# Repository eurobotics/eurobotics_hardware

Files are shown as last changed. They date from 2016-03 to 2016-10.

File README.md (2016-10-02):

# EuRobotics Engineering Hardware
Hardware del equipo Eurobotics Engineering para el desarrollo de robots participantes en Eurobot.

<p align="center">
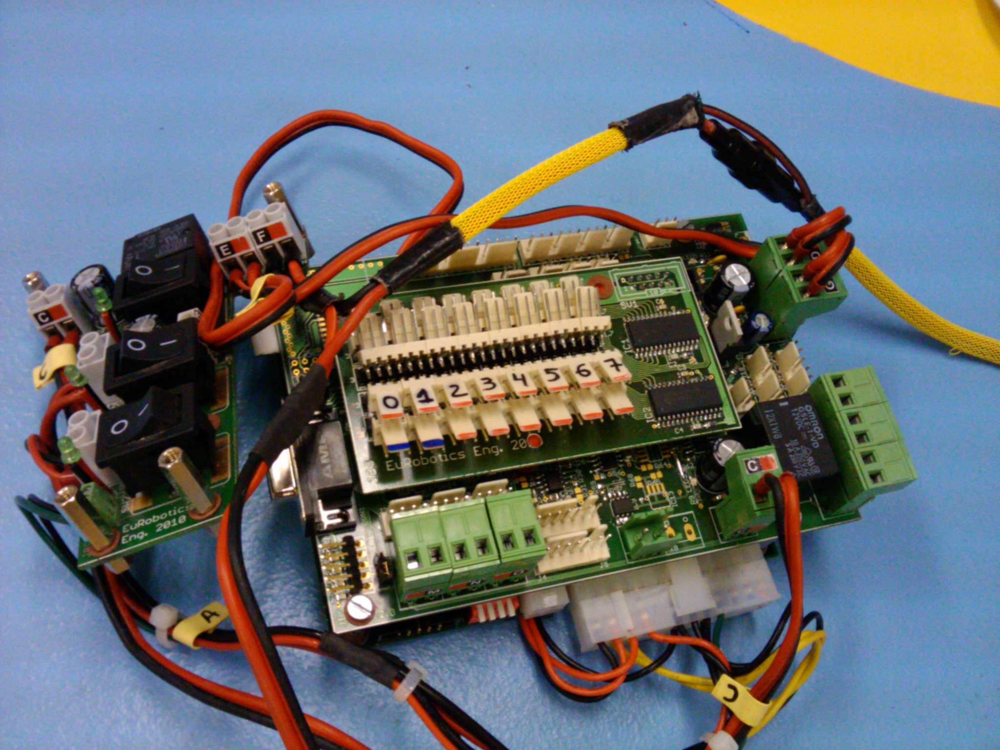
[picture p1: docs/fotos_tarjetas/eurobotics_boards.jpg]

</p>

## Organización

 - Cada carpeta del repositorio se corresponde con una tarjeta.

 - En el root de cada capeta se encuentra el proyecto de desarrollo de la tarjeta (Eagle, Orcad, Altium...). Si es una tarjeta comercial la documentación dada por el fabricante.

 - Por lo general, los archivos de cada proyecto se nombran como MMMMM_rXX, donde XX es la revisión y MMMMM el nombre de la tarjeta. La modificaciones sobre tarjetas fabricadas se documentan añadiendo al nombre del fichero de diseño el sufijo _NNNN_rYY_, donde NNNN es el identificador de la modificacion y YY es el número revisión de la modificación. Por ejemplo: "mainboard_r15_eurobot2012_r1.pdf" es la modificación para eurobot 2012 con revisión 1 de la tarjeta mainboard correspondientes a la revisión 15 de los esquemas.

 - Cada carpeta de una tarjeta desarrollada puede contener las siguientes subcarpetas:
   + bom: listado de materiales.
   + cam: ficheros de fabricación y versión en pdf de versiones de tarjetas fabricadas o de modificaciones en placa realizadas para una edición concreta de Eurobot.

## dsPIC Protoboard

Tarjeta prototipo basada en microcontrolador dspic33. Desarrollada para Eurobot 2010. Diseñada en Eagle (sólo esquematicos). Fabricada sobre tarjeta de prototipos. Es la tarjeta que se utilizó en el robot prototipo, llamado Dumybot, con el que se portó las librerías Aversive.

<p align="center">
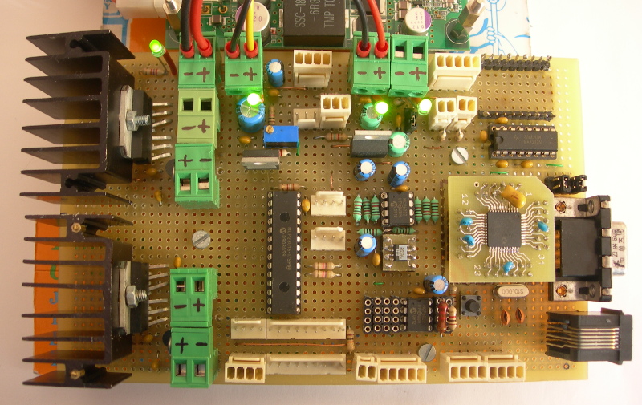
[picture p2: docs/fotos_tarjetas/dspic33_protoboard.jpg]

</p>

### Características

* Control motores: DC, Dunkermotoren, servos, AX12.
* Comunicaciones: RS-232, BT, SPI, I2C
* Sensores: industriales, TTL, laser analógico y encoders en cuadratura
* GPIOS: puerto de expansión I2C de 16 E/S.

### Autor

Javier Baliñas Santos

## Mainboard V01/V02

Tarjeta principal del robot. Compuesta por dos microcontroladores dspic33 comunicados por I2C, un maestro y un esclavo. El maestro está pensado para implementar la navegación motriz y estrategia del robot, y el
esclavo para controlar la mecánica del robot.

<p align="center">
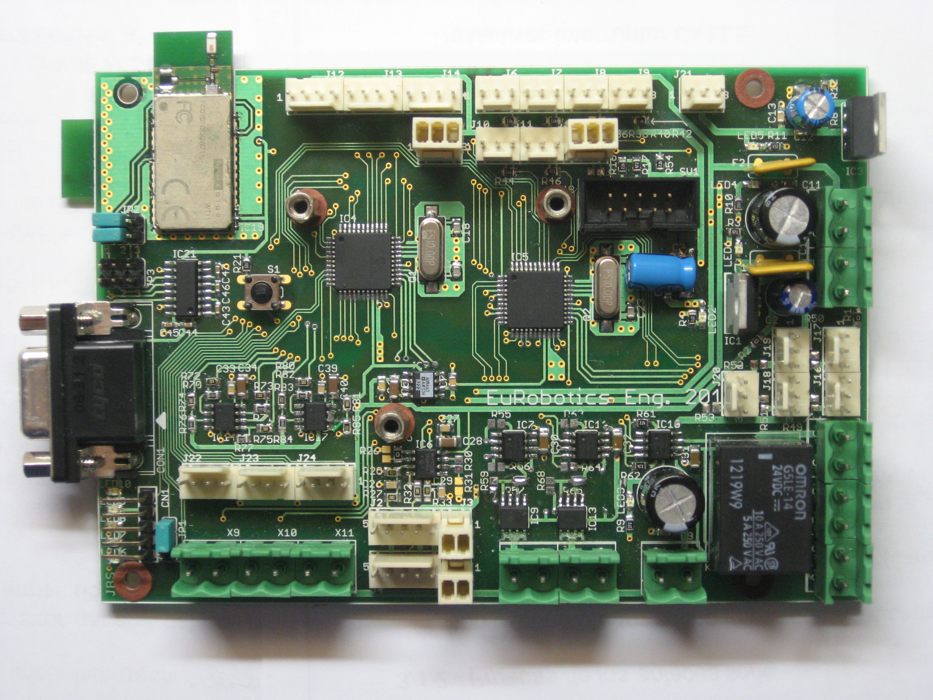
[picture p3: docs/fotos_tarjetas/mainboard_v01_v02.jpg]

</p>

Desarrollada para el robot de Eurobot 2010. Diseño en Eagle (esquemáticos y PCB). Tiene varios bugs documentados y solucionados en la versión 2.

La versión V02 de la tarjeta principal soluciona algunos errores de la versión V01. Desarrollada para Eurobot 2012 y utilizada en las ediciones posteriores.

### Características

* 3 motores Dunkermotoren
* 2 motores DC de 12V
* 1 solenoide 12V
* 1 relé
* 2 telémetros lásers
* 5 servos estándar
* 1 interfaz servos AX12
* 3 encoders con salida en cuadratura
* 7 sensores 12V
* 1 interfaz RS-232
* 2 interfaces Bluetooth (SPP)
* 1 conector para tarjeta de sensores _sensorboard_

### Autor

Javier Baliñas Santos

## Mainboard V03

Tercera versión de la tarjeta principal de los robots. Compuesta por un único un microcontrolador.

Desarrollada para Eurobot 2014 y utilizada en las ediciones posteriores.

<p align="center">
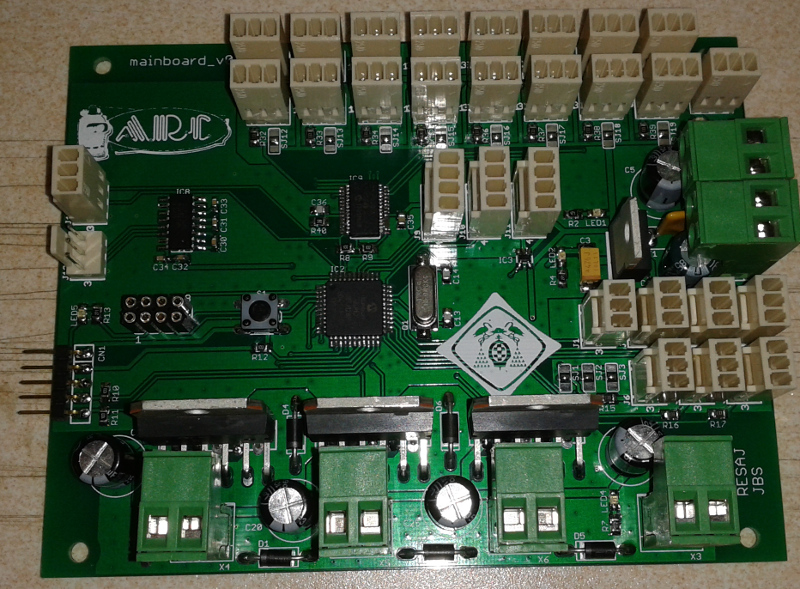
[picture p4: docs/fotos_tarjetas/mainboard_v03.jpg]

</p>

### Características
* 3 motores DC de 12V
* 4 servos estándar
* 1 interfaz servos AX12
* 2 encoders con salida en cuadratura
* 1 encoder con salida en cuadratura (módulo x4, sin decodificación de signo)
* 16 E/S de 12/5V
* 2 entradas de captura de tiempo
* 1 interfaz RS-232/Bluetooth
* 1 interfaz I2C
* 1 interfaz SPI

### Autores

Diseño electrónico: Javier Baliñas Santos  
Diseño PCB: Rubén Espino San José

## Sensorboard

Tarjeta de expansión E/S digital por I2C (32 E/S). Desarrollada para Eurobot 2010 y reutilizada en las siguientes ediciones.

<p align="center">
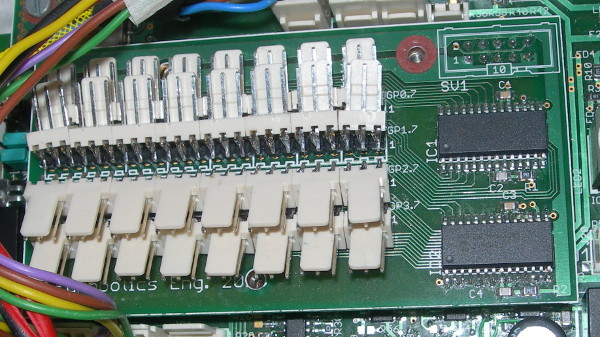
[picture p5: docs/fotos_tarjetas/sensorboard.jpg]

</p>

### Autor

Javier Baliñas Santos

## Swithboard

<p align="center">
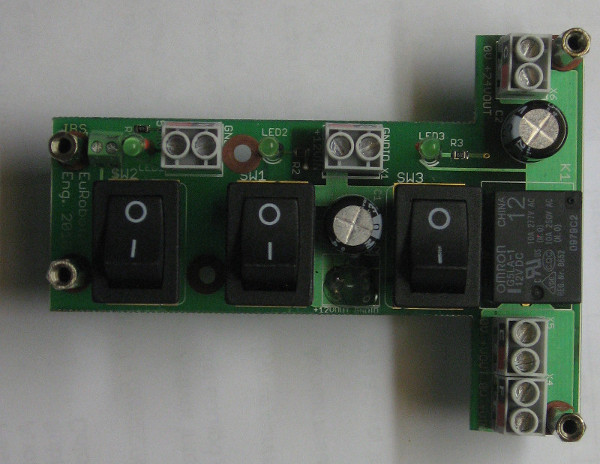
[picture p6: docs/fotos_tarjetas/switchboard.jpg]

</p>

Tarjeta de distribución de alimentación de los robots. Permite activar de forma independiente las diferentes alimentaciones del robot: 24V, 12V y 5V. Desarrollada para Eurobot 2010 y reutilizada en las siguientes ediciones. Diseño en Eagle (esquemáticos y PCB).

### Autor

Javier Baliñas Santos

## Beaconboard

Electrónica de la baliza desarrollada para Eurobot 2010 por Diego Salazar. Permite el control de 1 motor DC con encoder en cuadratura, la lectura de 2 sensores de tipo Keyence y de 2 sensores opticos de herradura. Permite la comunicación por Bluetooth. Tiene bugs resueltos en placa, pero no todos documentados. Diseño en Orcad (esquemas y PCB).

<p align="center">
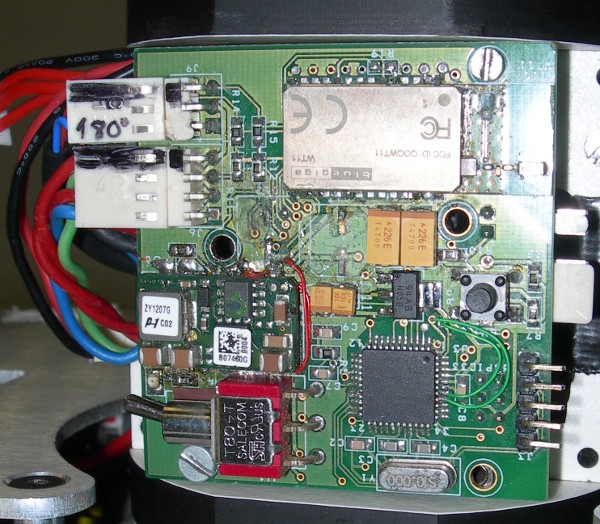
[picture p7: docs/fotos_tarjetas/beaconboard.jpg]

</p>

### Autor

Diego Salazar Arcucci

## Vacuumboard

Tarjeta de control de hasta 4 electrovalvulas y 4 bombas de vacio.

<p align="center">
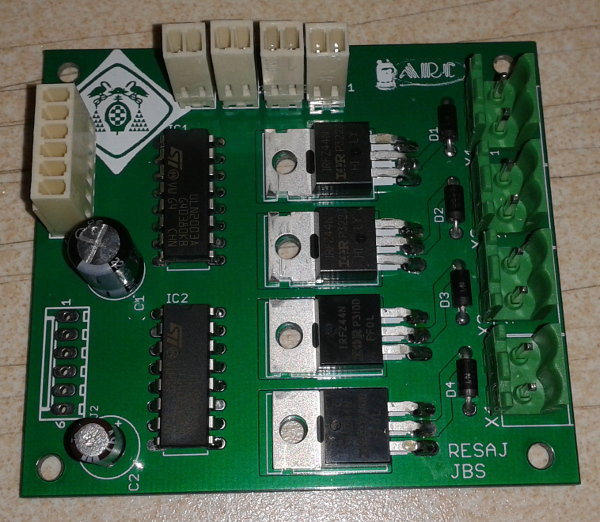
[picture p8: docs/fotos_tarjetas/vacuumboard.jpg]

</p>

### Autores

Diseño electrónico: Javier Baliñas Santos  
Diseño PCB: Rubén Espino San José

## M4 ATX

Fuente de alimentación mini ATX. Perminte un rango de alimentación variable y da salidas de +/-12V, 5V y 3.3V.  Se ha utilizado desde Eurobot 2010 para alimentar la electrónica del robot a partir de baterías. Es una tarjeta comercial.

<p align="center">
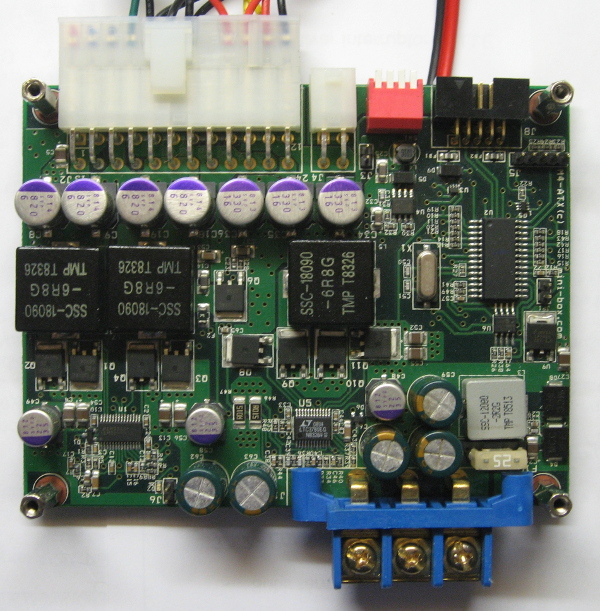
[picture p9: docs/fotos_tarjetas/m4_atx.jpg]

</p>

## Licencia

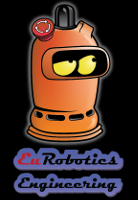
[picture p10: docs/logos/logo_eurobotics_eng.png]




Todos estos productos están liberados mediante [Creative Commons Attribution-ShareAlike 4.0 International License](http://creativecommons.org/licenses/by-sa/4.0/).  
_All these products are released under [Creative Commons Attribution-ShareAlike 4.0 International License](http://creativecommons.org/licenses/by-sa/4.0/)._

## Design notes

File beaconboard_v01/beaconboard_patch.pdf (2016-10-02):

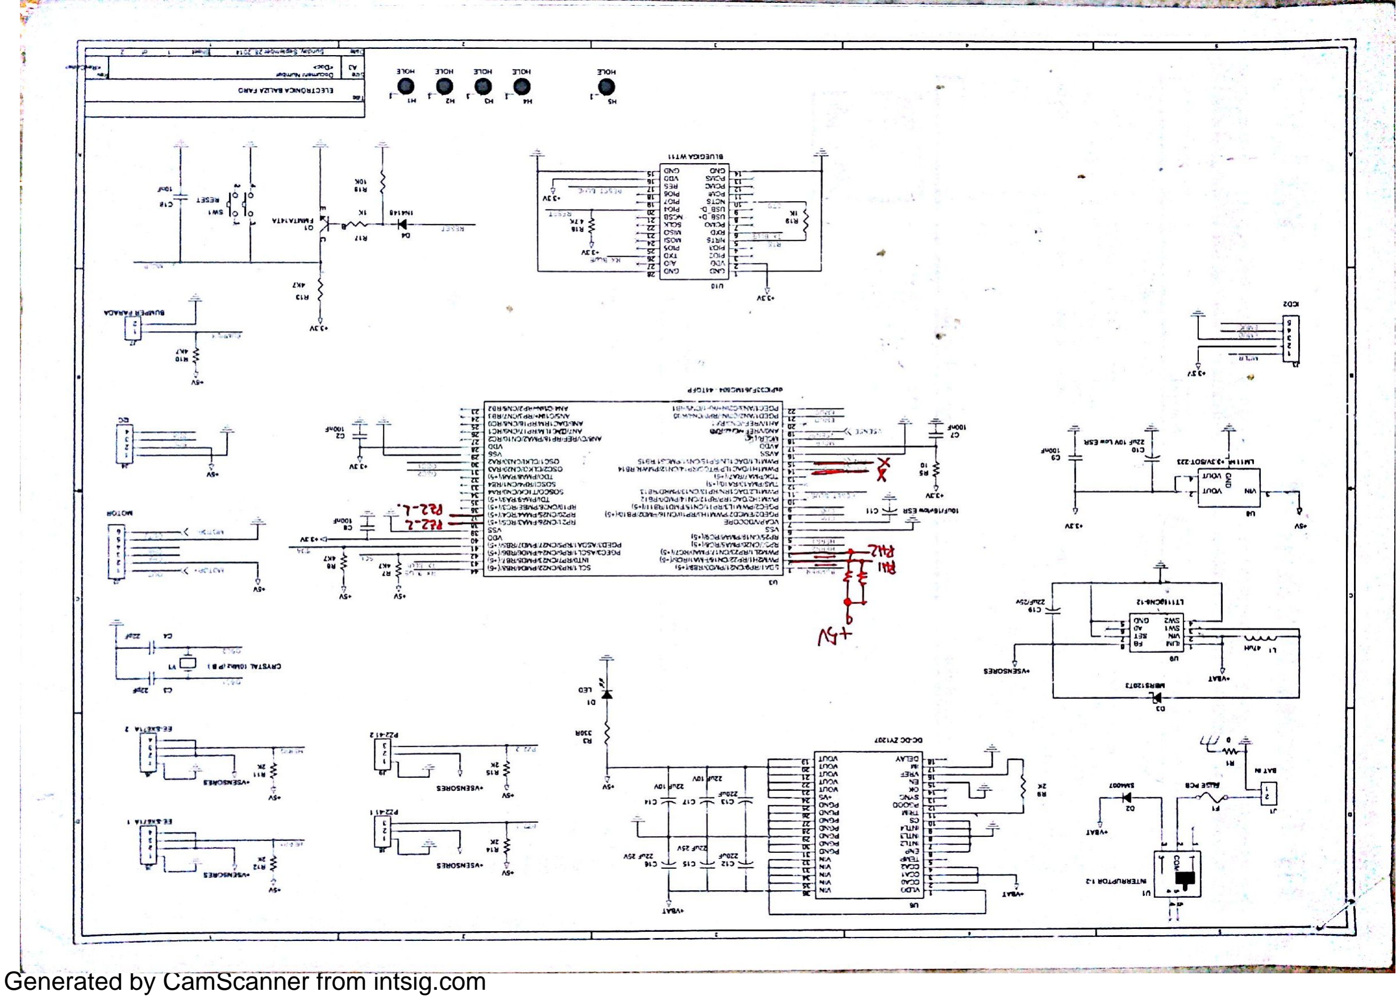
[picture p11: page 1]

Generated by CamScanner from intsig.com

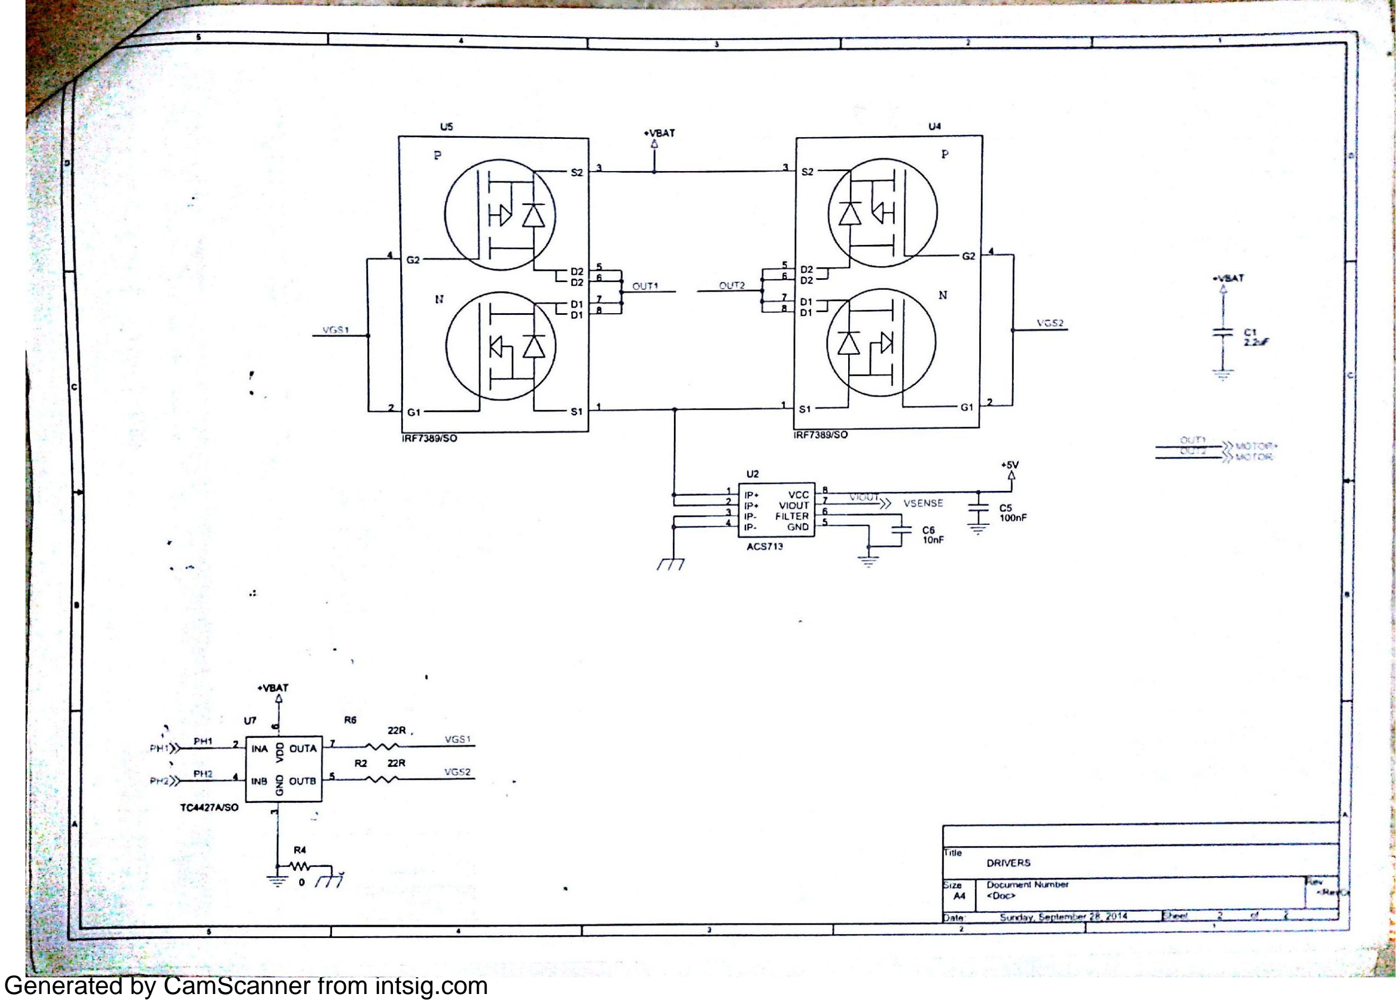
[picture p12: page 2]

Generated by CamScanner from intsig.com

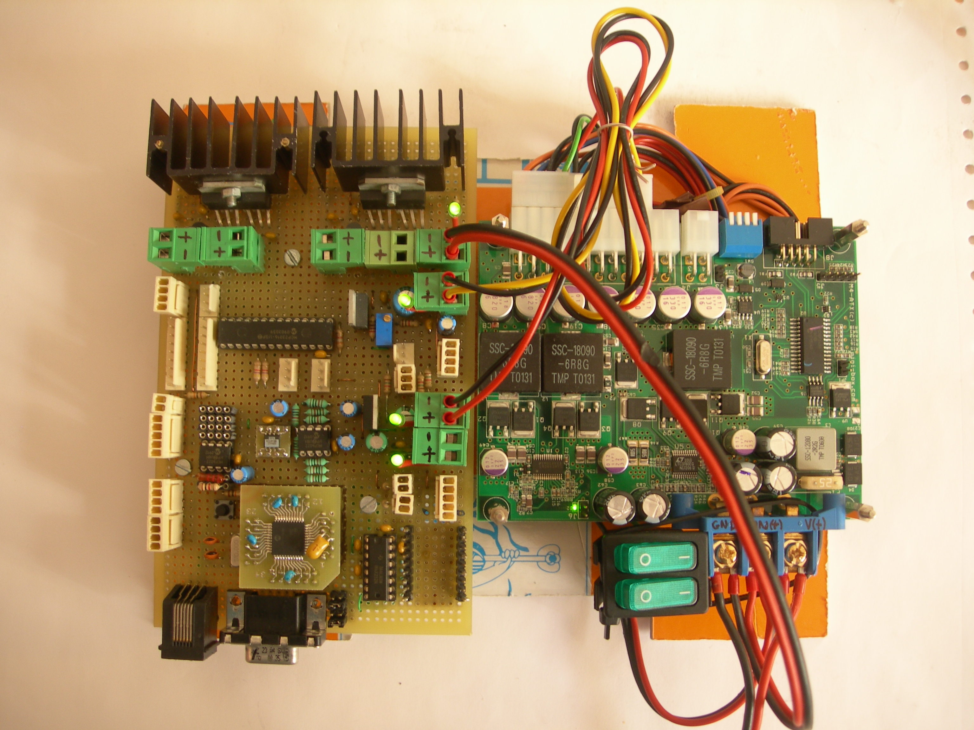
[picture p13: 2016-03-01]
dspic33_protoboard/cam/dvk_dspic33_protoboard.JPG

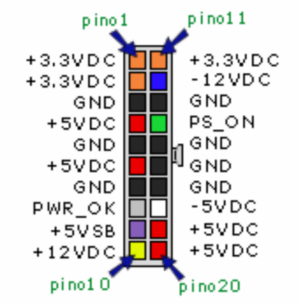
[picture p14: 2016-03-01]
m4_atx/conector_atx.png

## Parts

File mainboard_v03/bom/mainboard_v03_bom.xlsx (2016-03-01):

Qty | Parts | Columna1 | Value | Package | Description | Manufacturer | Manufacture Part # | Supplier | Supplier Part # | Min Qty | Price (EUR) | Ext. Qty | Ext. Price
1 | C1 |  | 220uF/10V | E2,5-7 | CONDENSADOR ELECTROLITICO / 10V / PASO 2.5mm |  |  | symbol |  |  |  | 1 | 0
8 | C10, C11, C12, C30, C31, C32, C33, C34 |  | 100nF | C0603 | CONDENSADOR CERAMICO / 50V / SMD 0603 |  |  |  |  |  |  | 8 | 0
2 | C13, C14 |  | 22pF | C0805 | CONDENSADOR CERAMICO / 50V / SMD 0805 |  |  |  |  |  |  | 2 | 0
3 | C15, C20, C25 |  | 220uF/48V | E3,5-10 | CONDENSADOR ELECTROLITICO / 48V / PASO 3.5mm |  |  | symbol |  |  |  | 3 | 0
3 | C16, C21, C26 |  | 220nF | C0805 | CONDENSADOR CERAMICO / 50V / SMD 0805 |  |  |  |  |  |  | 3 | 0
6 | C17, C18, C22, C23, C27, C28 |  | 15nF | C0805 | CONDENSADOR CERAMICO / 50V / SMD 0805 |  |  |  |  |  |  | 6 | 0
3 | C19, C24, C29 |  | 10nF | C0805 | CONDENSADOR CERAMICO / 50V / SMD 0805 |  |  |  |  |  |  | 3 | 0
5 | C2, C4, C6, C8, C35 |  | 100nF | C0805 | CONDENSADOR CERAMICO / 50V / SMD 0805 |  |  |  |  |  |  | 5 | 0
1 | C3 |  | 47uF/6V | SMC_D | CONDENSADOR TANTALO / 6V / SMD SMC-D |  |  | symbol |  |  |  | 1 | 0
1 | C36 |  | 33pF | C0805 | CONDENSADOR CERAMICO / 50V / SMD 0805 |  |  |  |  |  |  | 1 | 0
2 | C5, C7 |  | 220uF/35V | E5-10,5 | CONDENSADOR ELECTROLITICO / 35V / PASO 5mm |  |  | symbol |  |  |  | 2 | 0
1 | C9 |  | 10uF/6V/lowESR | SMC_A | CONDENSADOR TANTALO / 6V / SMD SMC-A |  |  | symbol |  |  |  | 1 | 0
1 | CN1 |  |  | SIP-100-5V | TIRA DE PINES MACHO ACODADA / PCB |  |  |  |  |  |  | 1 | 0
6 | D1, D2, D3, D4, D5, D6 |  | BYW100 | F126-10 | DIODO DE RECUPERACIÓN RÁPIDA |  |  |  |  |  |  | 6 | 0
2 | F1, F2 |  | FUSETE5 | TE5 | FUSIBLE REARMABLE / 1A / PASO 5mm |  |  |  |  |  |  | 2 | 0
1 | IC1 |  | LM1086CT-3.3 | 317TS | REGULADOR DE VOLTAJE |  |  |  |  |  |  | 1 | 0
1 | IC2 |  | DSPIC33FJ128MC804-I/PT | TQFP44 | MICROCONTROLADOR / TQFP44 |  |  |  |  |  |  | 1 | 0
1 | IC3 |  | SN74LVC1G86DBVR | SOT23-5 | PUERTA LOGICA XOR / SOT23 |  |  |  |  |  |  | 1 | 0
3 | IC4, IC5, IC6 |  | L6203 | MULTIWATT-11 | DRIVER PUENTE EN H MOSFET |  |  |  |  |  |  | 3 | 0
1 | IC7 |  | WT11A | WT11 | MODULO BLUETOOTH |  |  |  |  |  |  | 1 | 0
1 | IC8 |  | MAX232ACSE | SO16 | TRASNCEIVER RS-232 / SO16 |  |  |  |  |  |  | 1 | 0
1 | IC9 |  | MCP23016SS | SSOP28 | EXPANSON DE PUERTOS I2C / SSOP28 |  |  |  |  |  |  | 1 | 0
26 | J1, J2, J3, J4, J5, J6, J7, J8, J12, J13, J26, J27, J28, J29, J30, J31, J32, J33, J34, J35, J36, J37, J38, J39, J40, J41 |  |  | 6410-03 | CONECTOR MOLEX / 3 VIAS / PCB VERTICAL / PASO 2.54mm |  |  |  |  |  |  | 26 | 0
26 | J1, J2, J3, J4, J5, J6, J7, J8, J12, J13, J26, J27, J28, J29, J30, J31, J32, J33, J34, J35, J36, J37, J38, J39, J40, J41 |  |  | 6410-03 | CONECTOR MOLEX / 3 VIAS / CABLE / PASO 2.54mm |  |  |  |  |  |  | 26 | 0
3 | J9, J10, J11 |  | 22-27-2041-04 | 6410-04 | CONECTOR MOLEX / 4 VIAS / PCB VERTICAL / PASO 2.54mm |  |  |  |  |  |  | 3 | 0
5 | LED1, LED2, LED3, LED4, LED5 |  | Green | CHIP-LED0805 | LED VERDE / SMD 0805 |  |  |  |  |  |  | 5 | 0
1 | Q1 |  | 10MHz | HC49UP | CRYSTAL 10.000MHz / SMD HC49UP |  |  |  |  |  |  | 1 | 0
3 | R1, R3, R5 |  | 0R | R0805 | RESISTENCIA / 5% / 0.1W / SMD 0805 |  |  |  |  |  |  | 3 | 0
3 | R10, R11, R12 |  | 10K | R0805 | RESISTENCIA / 5% / 0.1W / SMD 0805 |  |  |  |  |  |  | 3 | 0
3 | R15, R16, R17 |  | 13K | R0805 | RESISTENCIA / 5% / 0.1W / SMD 0805 |  |  |  |  |  |  | 3 | 0
3 | R18, R20, R22 |  | 0R | M0805 | RESISTENCIA / 5% / 0.1W / SMD 0805 |  |  |  |  |  |  | 3 | 0
3 | R19, R21, R23 |  | 12R | M0805 | RESISTENCIA / 5% / 0.1W / SMD 0805 |  |  |  |  |  |  | 3 | 0
1 | R2 |  | 470R | R0805 | RESISTENCIA / 5% / 0.1W / SMD 0805 |  |  |  |  |  |  | 1 | 0
16 | R24, R25, R26, R27, R28, R29, R30, R31, R32, R33, R34, R35, R36, R37, R38, R39 |  |  | R0805 | RESISTENCIA / 5% / 0.1W / SMD 0805 |  |  |  |  |  |  | 16 | 0
2 | R4, R13 |  | 270R | R0805 | RESISTENCIA / 5% / 0.1W / SMD 0805 |  |  |  |  |  |  | 2 | 0
1 | R40 |  | 3K9 | R0805 | RESISTENCIA / 5% / 0.1W / SMD 0805 |  |  |  |  |  |  | 1 | 0
4 | R6, R8, R9, R14 |  | 1K | R0805 | RESISTENCIA / 5% / 0.1W / SMD 0805 |  |  |  |  |  |  | 4 | 0
1 | R7 |  | 2K7 | R0805 | RESISTENCIA / 5% / 0.1W / SMD 0805 |  |  |  |  |  |  | 1 | 0
1 | S1 |  |  | B3F-10XX | PULSADOR CUELLO CORTO / TIPO DPST (DOBLE CIRCUITO PULSACION ÚNICA) |  |  |  |  |  |  | 1 | 0
19 | SJ1, SJ2, SJ3, SJ4, SJ5, SJ6, SJ7, SJ8, SJ9, SJ10, SJ11, SJ12, SJ13, SJ14, SJ15, SJ16, SJ17, SJ18, SJ19 |  | 4K7 | SJ_2 | RESISTENCIA / 5% / 0.1W / SMD 0805 |  |  |  |  |  |  | 19 | 0
1 | SV1 |  | SPI/RF24 | MA04-2 | TIRA DE PINES HEMBRA / 2 FILAS X 4 PINES / PCB |  |  |  |  |  |  | 1 | 0
6 | X1, X2, X3, X4, X5, X6 |  |  | W237-132 | CONNECTOR TIPO CLEMA ENCHUFABLE / PCB VERTICAL / PASO 5.08mm |  |  |  |  |  |  | 6 | 0
6 | X1, X2, X3, X4, X5, X6 |  |  | W237-132 | CONNECTOR TIPO CLEMA ENCHUFABLE / CABLE / PASO 5.08mm |  |  |  |  |  |  | 6 | 0

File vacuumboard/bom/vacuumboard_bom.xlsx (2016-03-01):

Qty | Parts | Value | Package | Description | Manufacturer | Manufacture Part # | Supplier | Supplier Part # | Min Qty | Price (EUR) | Ext. Qty | Ext. Price
1 | C2 | 100uF 16V | E3,5-8 | CONDENSADOR ELECTROLITICO / 16V / PASO 3.5mm |  |  |  |  |  |  | 1 | 0
1 | C1 | 100uF 35V | E3,5-8 | CONDENSADOR ELECTROLITICO / 35V / PASO 3.5mm | MULTICOMP | MCMHR25V107M8X7 (http://es.farnell.com/multicomp/mcmhr25v107m8x7/capacitor-100uf-25v/dp/1871009) | FARNELL | 1871009 (http://es.farnell.com/multicomp/mcmhr25v107m8x7/capacitor-100uf-25v/dp/1871009) | 10 | 0.145 | 10 | 1.45
4 | D1, D2, D3, D4 | 1N5819 | DO41-7.6 | DIODO SCHOTTKY / DO-41 | HY ELECTRONICS | 1N5819 (http://es.farnell.com/hy-electronics/1n5819/schottky-diode-1a-40v-do-41/dp/1843511) | FARNELL | 1843511 (http://es.farnell.com/hy-electronics/1n5819/schottky-diode-1a-40v-do-41/dp/1843511) | 1 | 0.036 | 4 | 0.144
4 | R1, R2, R3, R4 | 20k | R0805 | RESISTENCIA / 5% / 0.1W / SMD 0805 |  |  |  |  |  |  | 4 | 0
4 | Q1, Q2, Q3, Q4 | IRFZ44 | TO220 | MOSFET / TO220 |  |  |  |  |  |  | 4 | 0
2 | IC1, IC2 | ULN2003AN | DIL16 | DRIVER ARRAY | TEXAS INSTRUMENTS | ULN2003AN (http://es.farnell.com/texas-instruments/uln2003an/transistor-array-npn-2003-dip16/dp/1470512) | FARNELL | 1470512 (http://es.farnell.com/texas-instruments/uln2003an/transistor-array-npn-2003-dip16/dp/1470512) | 1 | 0.5 | 2 | 1
1 | J1, J2 |  | 6410-06 | CONECTOR MOLEX / 6 VIAS / PCB VERTICAL / PASO 2.54mm |  |  |  |  |  |  | 1 | 0
1 | J1, J2 |  | 6410-06 | CONECTOR MOLEX / 6 VIAS / CABLE / PASO 2.54mm |  |  |  |  |  |  | 1 | 0
1 | J3, J4, J5, J6 |  | 6410-02 | CONECTOR MOLEX / 2 VIAS / PCB VERTICAL / PASO 2.54mm |  |  |  |  |  |  | 1 | 0
1 | J3, J4, J5, J6 |  | 6410-02 | CONECTOR MOLEX / 2 VIAS / CABLE / PASO 2.54mm |  |  |  |  |  |  | 1 | 0
4 | X1, X2, X3, X4 |  | MSTBA2 | CONNECTOR TIPO CLEMA ENCHUFABLE / PCB VERTICAL / PASO 5.08mm |  |  |  |  |  |  | 4 | 0
4 | X1, X2, X3, X4 |  | MSTBA2 | CONNECTOR TIPO CLEMA ENCHUFABLE / CABLE / PASO 5.08mm |  |  |  |  |  |  | 4 | 0

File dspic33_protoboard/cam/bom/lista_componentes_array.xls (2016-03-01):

Item | Qty | Value | Device | Parts | Description | Picture
1 | 3 | - | 22-27-2021-02 | J14, J15, J16 | Conector Molex 2 vías / Recto / Inserción PCB
2 | 2 | - | 22-27-2031-03 | J6, J7 | Conector Molex 3 vías / Recto / Inserción PCB
3 | 7 | - | 22-27-2041-04 | J1, J2, J3, J4, J5, J10, J11 | Conector Molex 4 vías / Recto / Inserción PCB
4 | 2 | - | 22-27-2051-05 | J12, J13 | Conector Molex 5 vías / Recto / Inserción PCB
5 | 2 | - | 22-27-2091-09 | J8, J9 | Conector Molex 9 vías / Recto / Inserción PCB
6 | 1 | - | 520470-3 | J17 | Conector tipo RJ11 6 vías / Acodado / Inserción PCB
7 | 1 | - | DB9F/90 | CON1 | Conector DB9 hembra / Acodado / Inserción PCB
8 | 3 | - | JP2E | JP1, JP2, JP3 | Tira de pines macho / Paso 2.54mm / Inserción PCB
10 | 8 | - | W237-02P | X1, X2, X3, X4, X5, X6, X7, X8 | Conector tipo clema conectable / Recto / Paso 5.08mm / Inserción PCB
11 | 8 | - |  | X1, X2, X3, X4, X5, X6, X7, X8 | Cabeza enchufable en conector tipo clema
14 | 1 | 1.43K/1% | R-US_0309/10 | R40 | Resistencia 1/4W / 1% / Inserción PCB
15 | 1 | 1K | R-US_0309/10 | R5 | Resistencia 1/4W / 5% / Inserción PCB
16 | 4 | 1K2 | R-US_0309/10 | R10, R11, R18, R19 | Resistencia 1/4W / 5% / Inserción PCB
17 | 3 | 1K5 | R-US_0207/7 | R28, R29, R30 | Resistencia 1/4W / 5% / Inserción PCB
18 | 1 | 3K9 | R-US_0207/7 | R33 | Resistencia 1/4W / 5% / Inserción PCB
19 | 2 | 4K7 | R-US_0207/7 | R31, R32 | Resistencia 1/4W / 5% / Inserción PCB
20 | 1 | 10K | R-US_0204/7 | R41 | Resistencia 1/4W / 5% / Inserción PCB
21 | 3 | 10K | R-US_0207/7 | R35, R44, R45 | Resistencia 1/4W / 5% / Inserción PCB
22 | 11 | 10K/1% | R-US_0309/10 | R9, R13, R14, R15, R21, R23, R24, R25, R34, R36, R38 | Resistencia 1/4W / 1% / Inserción PCB
23 | 1 | 10MHz | CRYSTALHC49U-H | Q1 | Cristal 10MHz / 50ppm / Perfil bajo / Inserción PCB
24 | 1 | 10R | R-US_0207/7 | R43 | Resistencia 1/4W / 5% / Inserción PCB
25 | 2 | 10nF | C-EU050-024X044 | C15, C20 | Condensador cerámico / 50V / Inserción PCB
26 | 2 | 10uF/10V | CPOL-USE3.5-10 | C11, C24 | Condensador electrolítico / 10V / Inserción PCB
27 | 1 | 10uF/16V | CPOL-USE3.5-8 | C37 | Condensador electrolítico / 16V / Inserción PCB
28 | 1 | 10uF/16V/lowESR | CPOL-USE3.5-8 | C32 | Condensador de tántalo de bajo ESR / 16V / Inserción PCB
29 | 2 | 12R | R-US_0309/10 | R12, R22
30 | 2 | 15K/1% | R-US_0309/10 | R8, R20 | Resistencia 1/4W / 1% / Inserción PCB
31 | 4 | 15nF | C-EU050-024X044 | C12, C16, C18, C21 | Condensador cerámico / 50V / Inserción PCB
32 | 2 | 22pF | C-EU050-024X044 | C34, C35 | Condensador cerámico / 50V / Inserción PCB
33 | 1 | 33pF | C-EU050-024X044 | C23 | Condensador cerámico / 50V / Inserción PCB
34 | 3 | 47uF/10V | CPOL-USE2-5 | C1, C3, C7 | Condensador electrolítico / 10V / Inserción PCB
35 | 17 | 100nF | C-EU050-024X044 | C2, C4, C6, C8, C13, C22, C25, C26, C27, C28, C29, C30, C31, C33, C36, C38, C39 | Condensador cerámico / 50V / Inserción PCB
36 | 1 | 187R/1% | R-US_0207/7 | R39 | Resistencia 1/4W / 1% / Inserción PCB
37 | 2 | 220nF | C-EU050-024X044 | C14, C19 | Condensador cerámico / 50V / Inserción PCB
38 | 4 | 220uF/48V | CPOL-USE2-5 | C5, C10, C17,C9 | Condensador electrolítico / 48V / Inserción PCB
39 | 1 | 240R | R-US_0309/10 | R4 | Resistencia 1/4W / 5% / Inserción PCB
40 | 1 | 500R | R-TRIMMT93YA | R6 | Potenciómetro multivuelta / Ajuste vertical / Inserción PCB
41 | 4 | BYW100 | BYW100 | D1, D2, D3, D4 | Diodo de recuperación rápida / Inserción PCB
42 | 4 | Zócalo | DSPIC33FJXXMC804SMD | IC11 | Tira de pines hembra / Paso 2.54mm / Inserción PCB
43 | 1 | DT6 | DT6 | S1 | Pulsador de cuello corto / Inserción PCB
44 | 8 | L6203 | L6203 | IC3, IC5 | Driver en puente en H
45 | 1 | Zócalo | MAX232 | IC8 | Zócalo DIP16 / Pin torneado
46 | 2 | Zócalo | OPA2344P | IC4, IC7 | Zócalo DIP8 / Pin torneado
47 | 1 | Zócalo | MCP32016 | IC6 | Zócalo DIP28 / Ancho 300mils / Pin torneado
48 | 2 | 5K |  | R? | Potenciómetro multivuelta / Ajuste vertical / Inserción PCB
49 | 3 | 74HC14 |  | IC? | Inversor trigger schmith / Formato DIP / Inserción PCB
50 | 2 | Conector ATX |  | X? | Conector hembra ATX acodado para PCB 24 vías/ Paso 4.20mm
51 | 2 | 12V-ATX |  | X1? | Conector hembra ATX acodado para PCB 4 vías / Paso 4.20mm
52 | 3 | Tarjeta wrapping |  | - | Tarjeta “wrapping” / 100x160mm

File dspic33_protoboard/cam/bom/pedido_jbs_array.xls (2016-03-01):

Item | Qty | Value | Parts | Description | Picture
1 | 3 | - | J14, J15, J16 | Conector Molex 2 vías / Recto / Inserción PCB
2 | 2 | - | J6, J7 | Conector Molex 3 vías / Recto / Inserción PCB
3 | 7 | - | J1, J2, J3, J4, J5, J10, J11 | Conector Molex 4 vías / Recto / Inserción PCB
4 | 2 | - | J12, J13 | Conector Molex 5 vías / Recto / Inserción PCB
5 | 2 | - | J8, J9 | Conector Molex 9 vías / Recto / Inserción PCB
6 | 1 | - | J17 | Conector tipo RJ11 6 vías / Acodado / Inserción PCB
7 | 1 | - | CON1 | Conector DB9 hembra / Acodado / Inserción PCB
8 | 3 | - | JP1, JP2, JP3 | Tira de pines macho / Paso 2.54mm / Inserción PCB
10 | 8 | - | X1, X2, X3, X4, X5, X6, X7, X8 | Conector tipo clema conectable / Recto / Paso 5.08mm / Inserción PCB
11 | 8 | - | X1, X2, X3, X4, X5, X6, X7, X8 | Cabeza enchufable en conector tipo clema
14 | 1 | 1.43K/1% | R40 | Resistencia 1/4W / 1% / Inserción PCB
15 | 1 | 1K | R5 | Resistencia 1/4W / 5% / Inserción PCB
16 | 4 | 1K2 | R10, R11, R18, R19 | Resistencia 1/4W / 5% / Inserción PCB
17 | 3 | 1K5 | R28, R29, R30 | Resistencia 1/4W / 5% / Inserción PCB
18 | 1 | 3K9 | R33 | Resistencia 1/4W / 5% / Inserción PCB
19 | 2 | 4K7 | R31, R32 | Resistencia 1/4W / 5% / Inserción PCB
20 | 1 | 10K | R41 | Resistencia 1/4W / 5% / Inserción PCB
21 | 3 | 10K | R35, R44, R45 | Resistencia 1/4W / 5% / Inserción PCB
22 | 11 | 10K/1% | R9, R13, R14, R15, R21, R23, R24, R25, R34, R36, R38 | Resistencia 1/4W / 1% / Inserción PCB
23 | 1 | 10MHz | Q1 | Cristal 10MHz / 50ppm / Perfil bajo / Inserción PCB
24 | 1 | 10R | R43 | Resistencia 1/4W / 5% / Inserción PCB
25 | 2 | 10nF | C15, C20 | Condensador cerámico / 50V / Inserción PCB
26 | 2 | 10uF/10V | C11, C24 | Condensador electrolítico / 10V / Inserción PCB
27 | 1 | 10uF/16V | C37 | Condensador electrolítico / 16V / Inserción PCB
28 | 1 | 10uF/16V/lowESR | C32 | Condensador de tántalo de bajo ESR / 16V / Inserción PCB
29 | 2 | 12R | R12, R22
30 | 2 | 15K/1% | R8, R20 | Resistencia 1/4W / 1% / Inserción PCB
31 | 4 | 15nF | C12, C16, C18, C21 | Condensador cerámico / 50V / Inserción PCB
32 | 2 | 22pF | C34, C35 | Condensador cerámico / 50V / Inserción PCB
33 | 1 | 33pF | C23 | Condensador cerámico / 50V / Inserción PCB
34 | 3 | 47uF/10V | C1, C3, C7 | Condensador electrolítico / 10V / Inserción PCB
35 | 17 | 100nF | C2, C4, C6, C8, C13, C22, C25, C26, C27, C28, C29, C30, C31, C33, C36, C38, C39 | Condensador cerámico / 50V / Inserción PCB
36 | 1 | 187R/1% | R39 | Resistencia 1/4W / 1% / Inserción PCB
37 | 2 | 220nF | C14, C19 | Condensador cerámico / 50V / Inserción PCB
38 | 4 | 220uF/48V | C5, C10, C17,C9 | Condensador electrolítico / 48V / Inserción PCB
39 | 1 | 240R | R4 | Resistencia 1/4W / 5% / Inserción PCB
40 | 1 | 500R | R6 | Potenciómetro multivuelta / Ajuste vertical / Inserción PCB
41 | 4 | BYW100 | D1, D2, D3, D4 | Diodo de recuperación rápida / Inserción PCB
42 | 4 | Zócalo | IC11 | Tira de pines hembra / Paso 2.54mm / Inserción PCB
43 | 1 | DT6 | S1 | Pulsador de cuello corto / Inserción PCB
44 | 8 | L6203 | IC3, IC5 | Driver en puente en H
45 | 1 | Zócalo | IC8 | Zócalo DIP16 / Pin torneado
46 | 2 | Zócalo | IC4, IC7 | Zócalo DIP8 / Pin torneado
47 | 1 | Zócalo | IC6 | Zócalo DIP28 / Ancho 300mils / Pin torneado
48 | 2 | 5K | R? | Potenciómetro multivuelta / Ajuste vertical / Inserción PCB
49 | 3 | 74HC14 | IC? | Inversor trigger schmith / Formato DIP / Inserción PCB
52 | 3 | Tarjeta wrapping | - | Tarjeta “wrapping” / 100x160mm

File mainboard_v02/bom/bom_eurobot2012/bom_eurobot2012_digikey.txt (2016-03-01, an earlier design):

Digi-Key Part No.	Manufacturer Name	Mfr Part No.	Customer Reference	Qty1	Qty2	Qty3
478-3351-1-ND			C1, C4, C6, C7, C9, C11, C13, C27, C33, C35, C36, C37, C38, C39, C41, C42, C26, C29	20		
P5124-ND			C2	1		
445-1602-1-ND			C5, C28, C34, C40	10		
493-1082-ND			C8, C10	2		
718-1090-1-ND			C3, C12	2		
399-1099-1-ND			C14, C16, C19, C20, C22, C25, C43, C44, C45, C46, C47	20		
478-3134-1-ND			C15, C21	2		
709-1172-1-ND			C17, C18, C23, C24	4		
478-1392-1-ND			C26, C29	10		
587-1352-1-ND			C30, C31, C32	10		
SS24FSCT-ND			D1, D2	2		
RUSBF120-ND			F1, F2	2		
497-3450-5-ND			IC1	1		
DSPIC33FJ128MC804-I/PT-ND			IC4, IC5	4		
MCP6022-E/SN-ND			IC6, IC14, IC17	3		
TC4427ACOA-ND			IC7, IC10, IC11	3
IRF7389PBFCT-ND			IC8, IC9, IC12, IC13	4
ICL3232IBNZ-ND			IC21	1
G5LE-1-VDDC12-ND			K1	1
160-1423-1-ND			LED1, LED2, LED3, LED4, LED5	5
160-1422-1-ND			LED6, LED7, LED8, LED9, LED10	5
631-1011-1-ND			Q1, Q2	2
RMCF1/10470JRCT-ND			R3	1
RMCF1/10270JRCT-ND			R4, R14, R15, R18, R19, R23	6
RHM240CCT-ND			R8	10
RMCF1/102.7KJRCT-ND			R9	1
RMCF1/101KJRCT-ND			R10, R11	2
RHM1.60KCRCT-ND			R12	10
RMCF1/104.7KJRCT-ND			R16, R17, R22, R29, R34, R36, R38, R40, R42, R44, R46, R48, R49, R50, R51, R52, R53, R54	18
RMCF1/1010KJRCT-ND			R21	1
RHM10.0KCRCT-ND			R27, R32	10
RHM4.30KCRCT-ND			R28, R33	10
RHM3.30KCRCT-ND			R25, R30	10
RHM1.10KCRCT-ND			R26, R31	10
RHM187CRCT-ND			R28, R33	10
RMCF1/100RCT-ND			R1, R2, R5, R6, R7, R13, R20, R24, R67, R79	10
RMCF1/102.2KJRCT-ND			R55, R56, R59, R60, R61, R62, R63, R64, R68, R69	10
311-22.0CRCT-ND			R57, R58, R65, R66	10
RHM20.0KCRCT-ND			R70, R71, R76, R77, R80, R84, R85	10
RHM10.0KCRCT-ND			R72, R73, R74, R75, R81, R82, R83	10
MCP23016-I/SO-ND			IC1, IC2	3

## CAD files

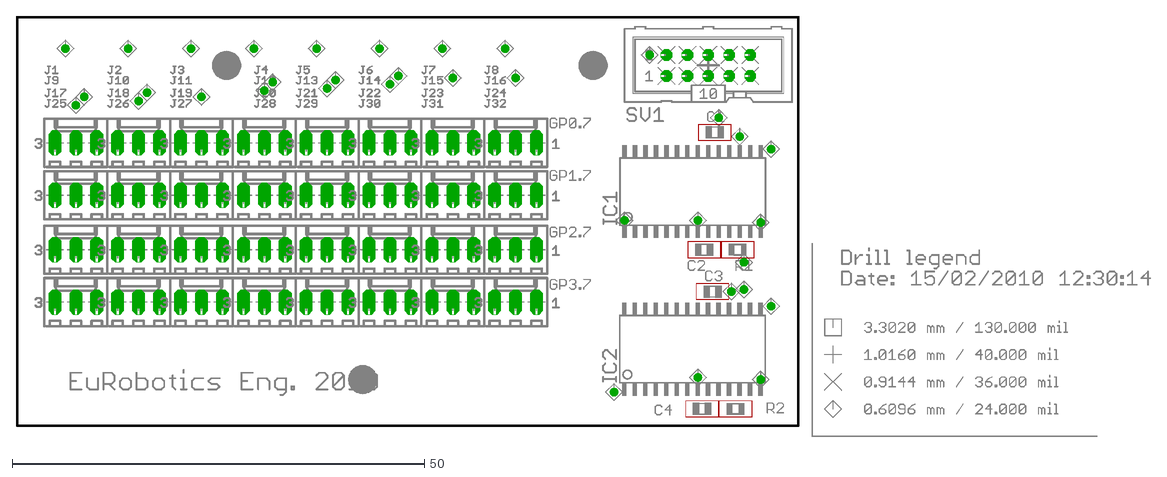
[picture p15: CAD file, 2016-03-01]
sensorboard/cam/sensorboard_eurobotics2010_r4.dxf
137.6 x 51.0

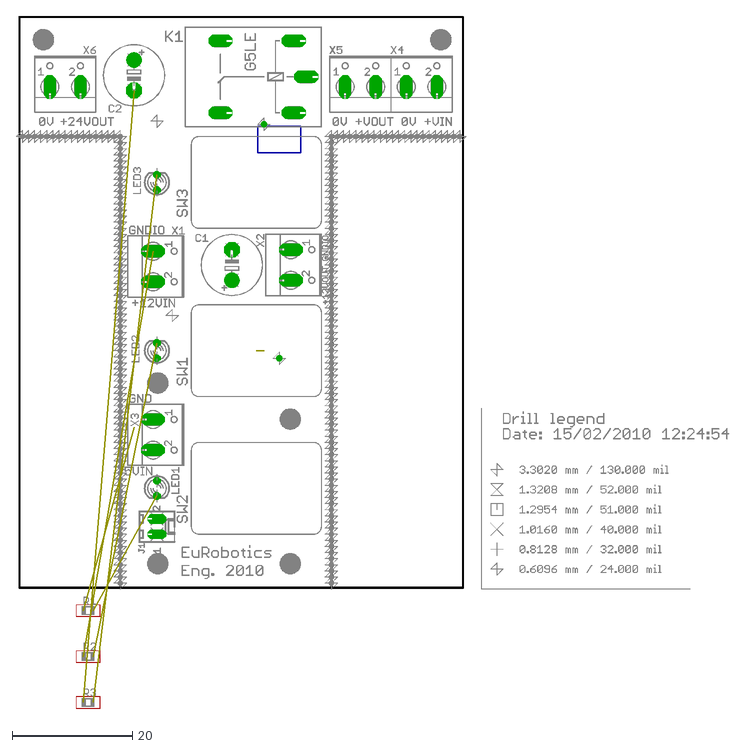
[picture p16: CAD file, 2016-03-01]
switchboard/cam/switchboard_eurobotics2010_r3.dxf
118.4 x 114.9

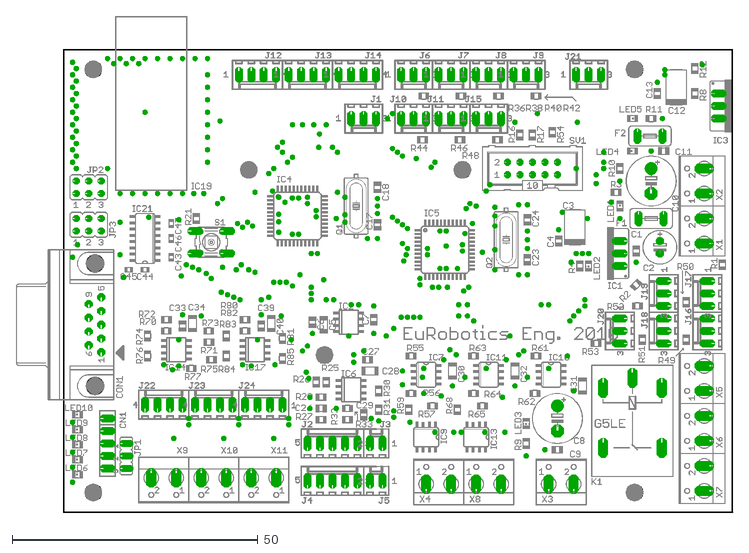
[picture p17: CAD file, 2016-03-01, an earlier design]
mainboard_v01/mainboard_eurobotics2010_r12.dxf
145.7 x 100.9

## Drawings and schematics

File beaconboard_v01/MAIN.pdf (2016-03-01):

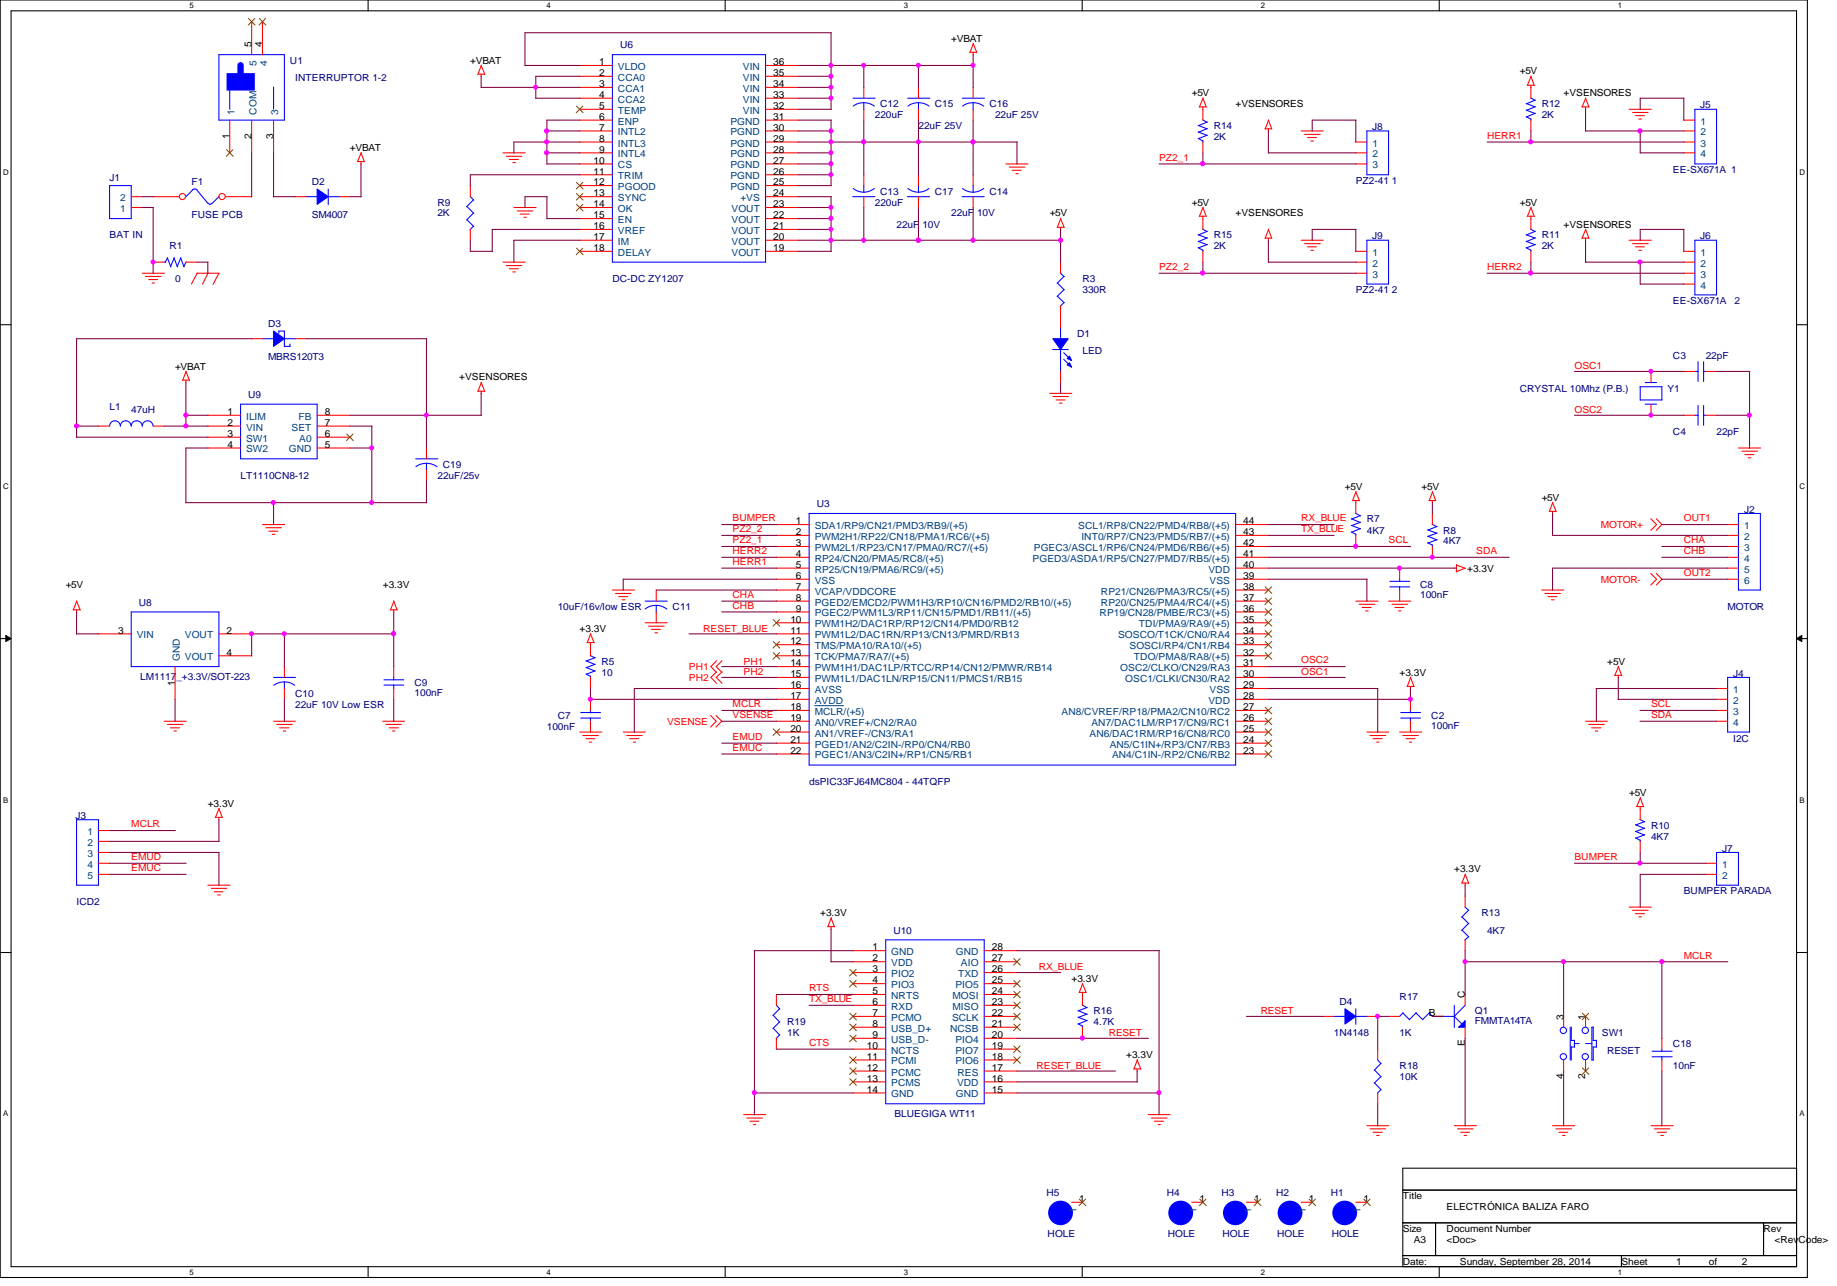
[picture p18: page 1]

3 | 34
4 | 33

9 | 28 | C13 | C17 | C14
10 | 27

Size A3 | Document Number | Rev

Date: Sunday, September 28, 2014 | Sheet 1 of 2

## +VBAT

P

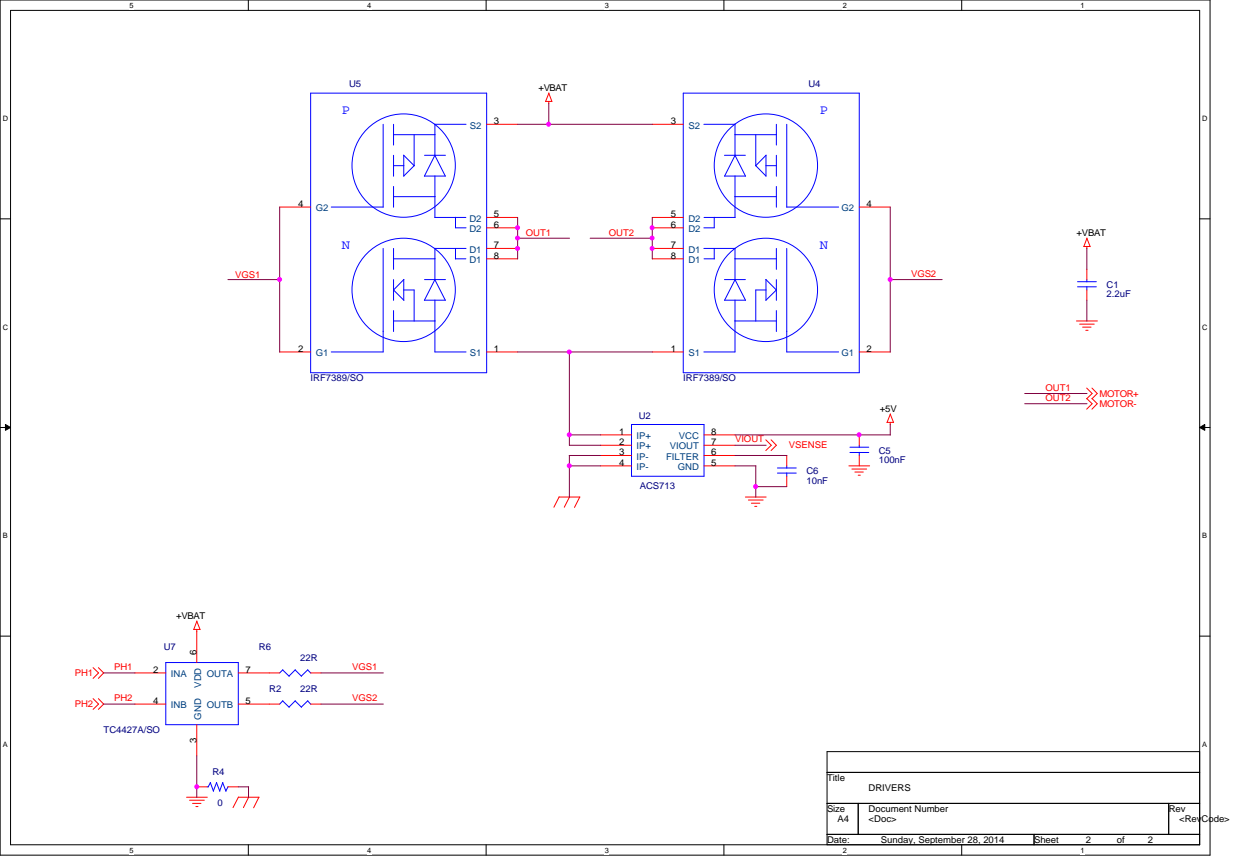
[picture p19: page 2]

Size A4 | Document Number | Rev

Date: Sunday, September 28, 2014 | Sheet 2 of 2

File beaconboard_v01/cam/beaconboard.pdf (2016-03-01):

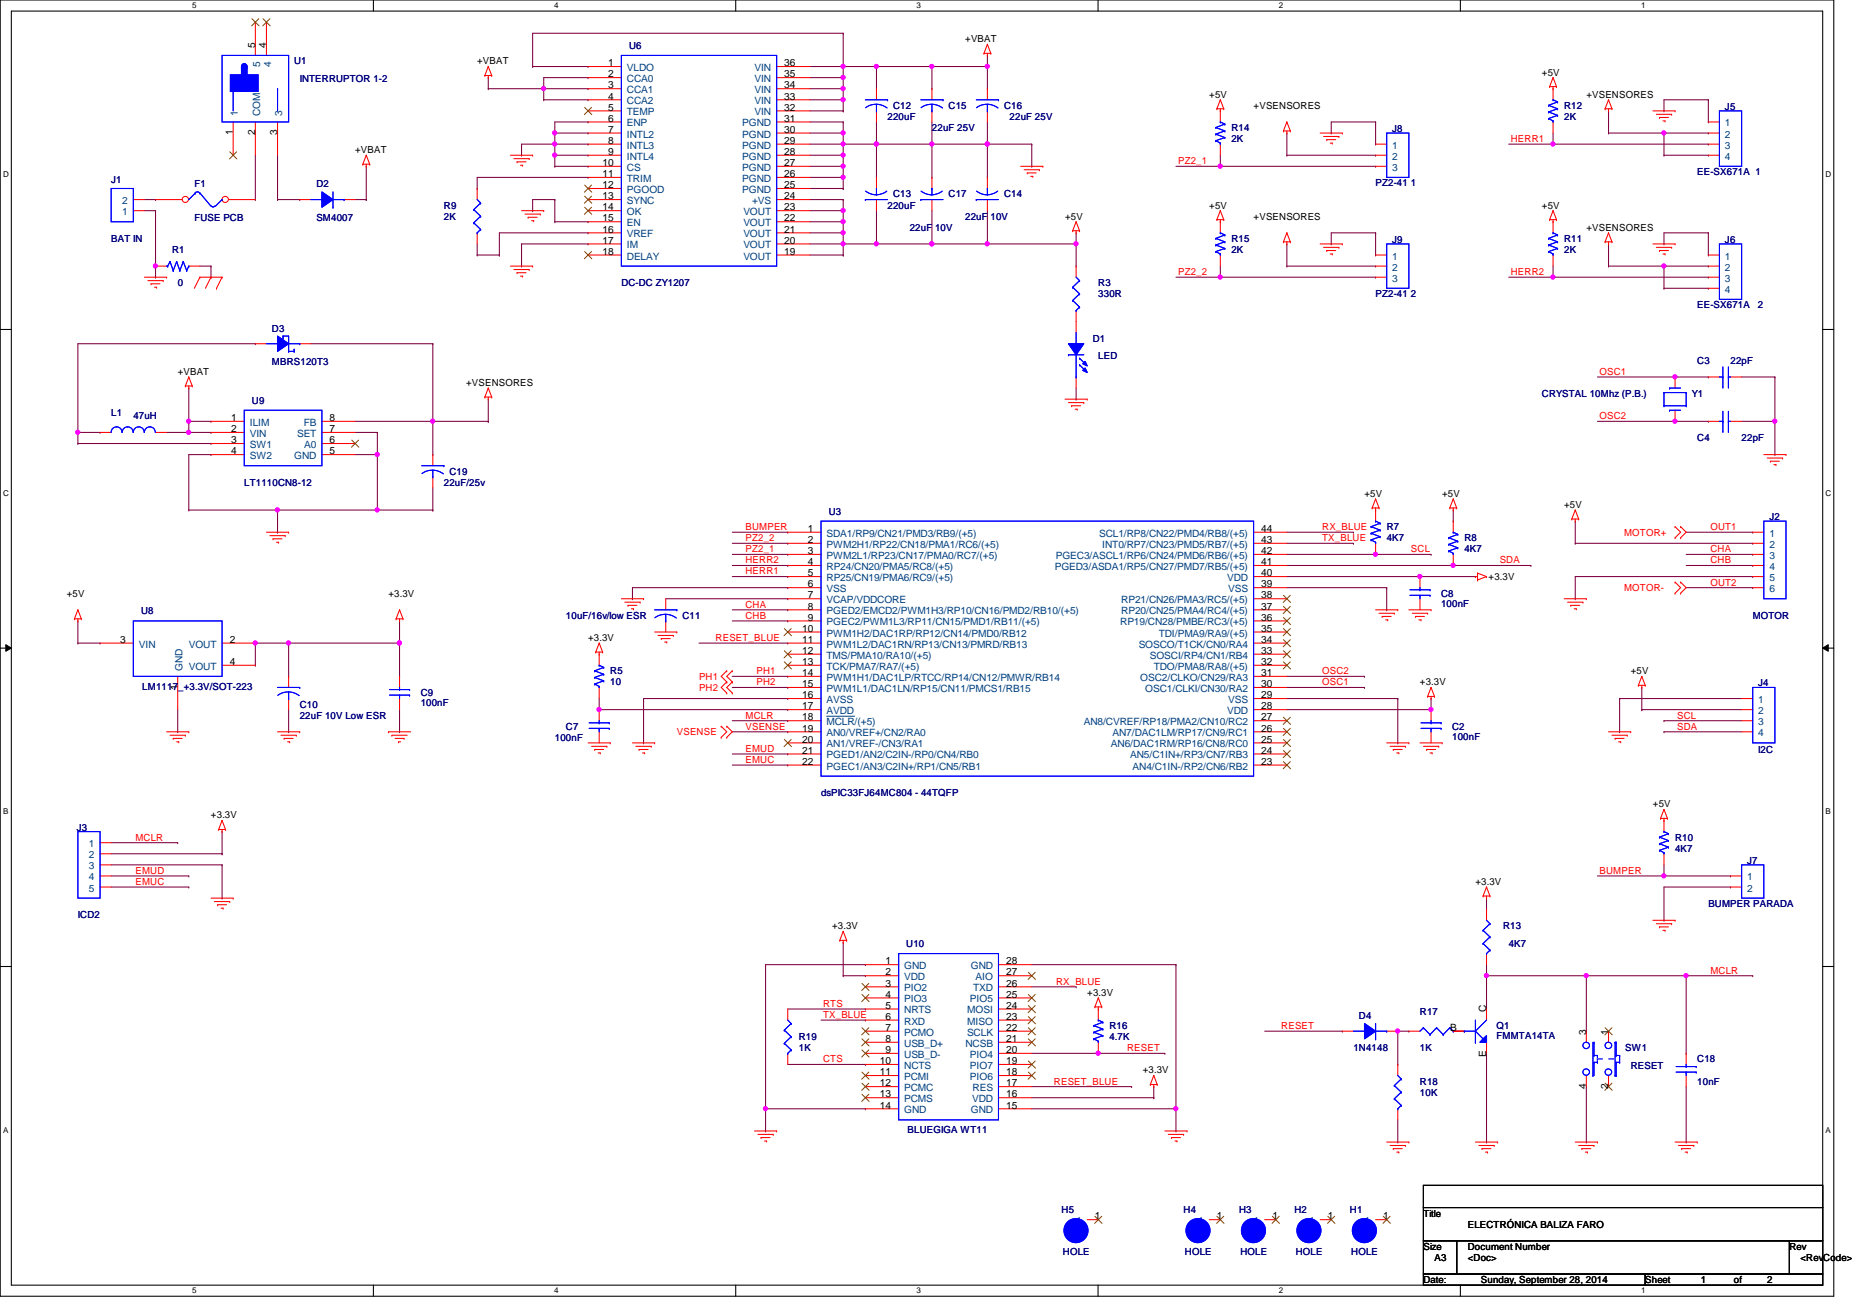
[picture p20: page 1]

5 | 4 | 3 | 2 | 1

## +VBAT

D2 5 | G2 4

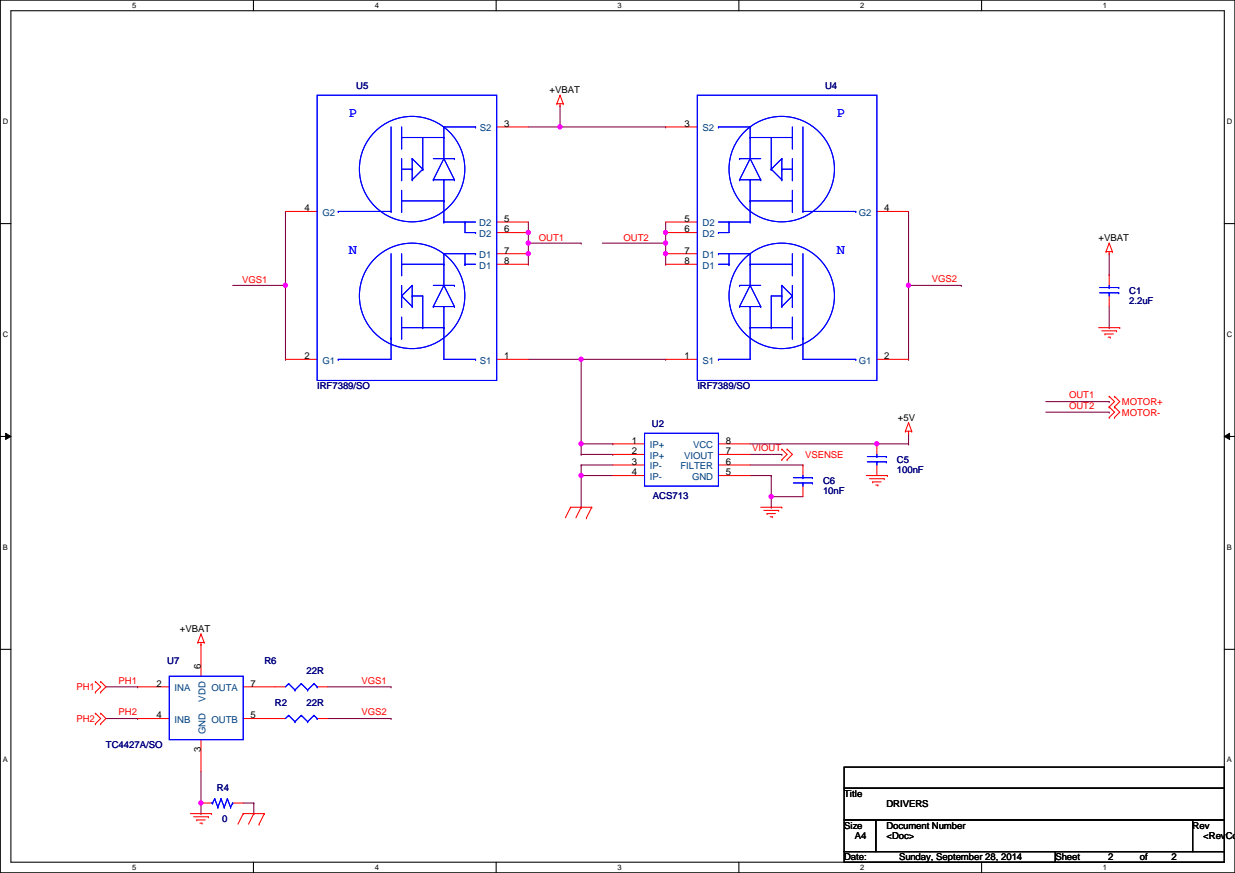
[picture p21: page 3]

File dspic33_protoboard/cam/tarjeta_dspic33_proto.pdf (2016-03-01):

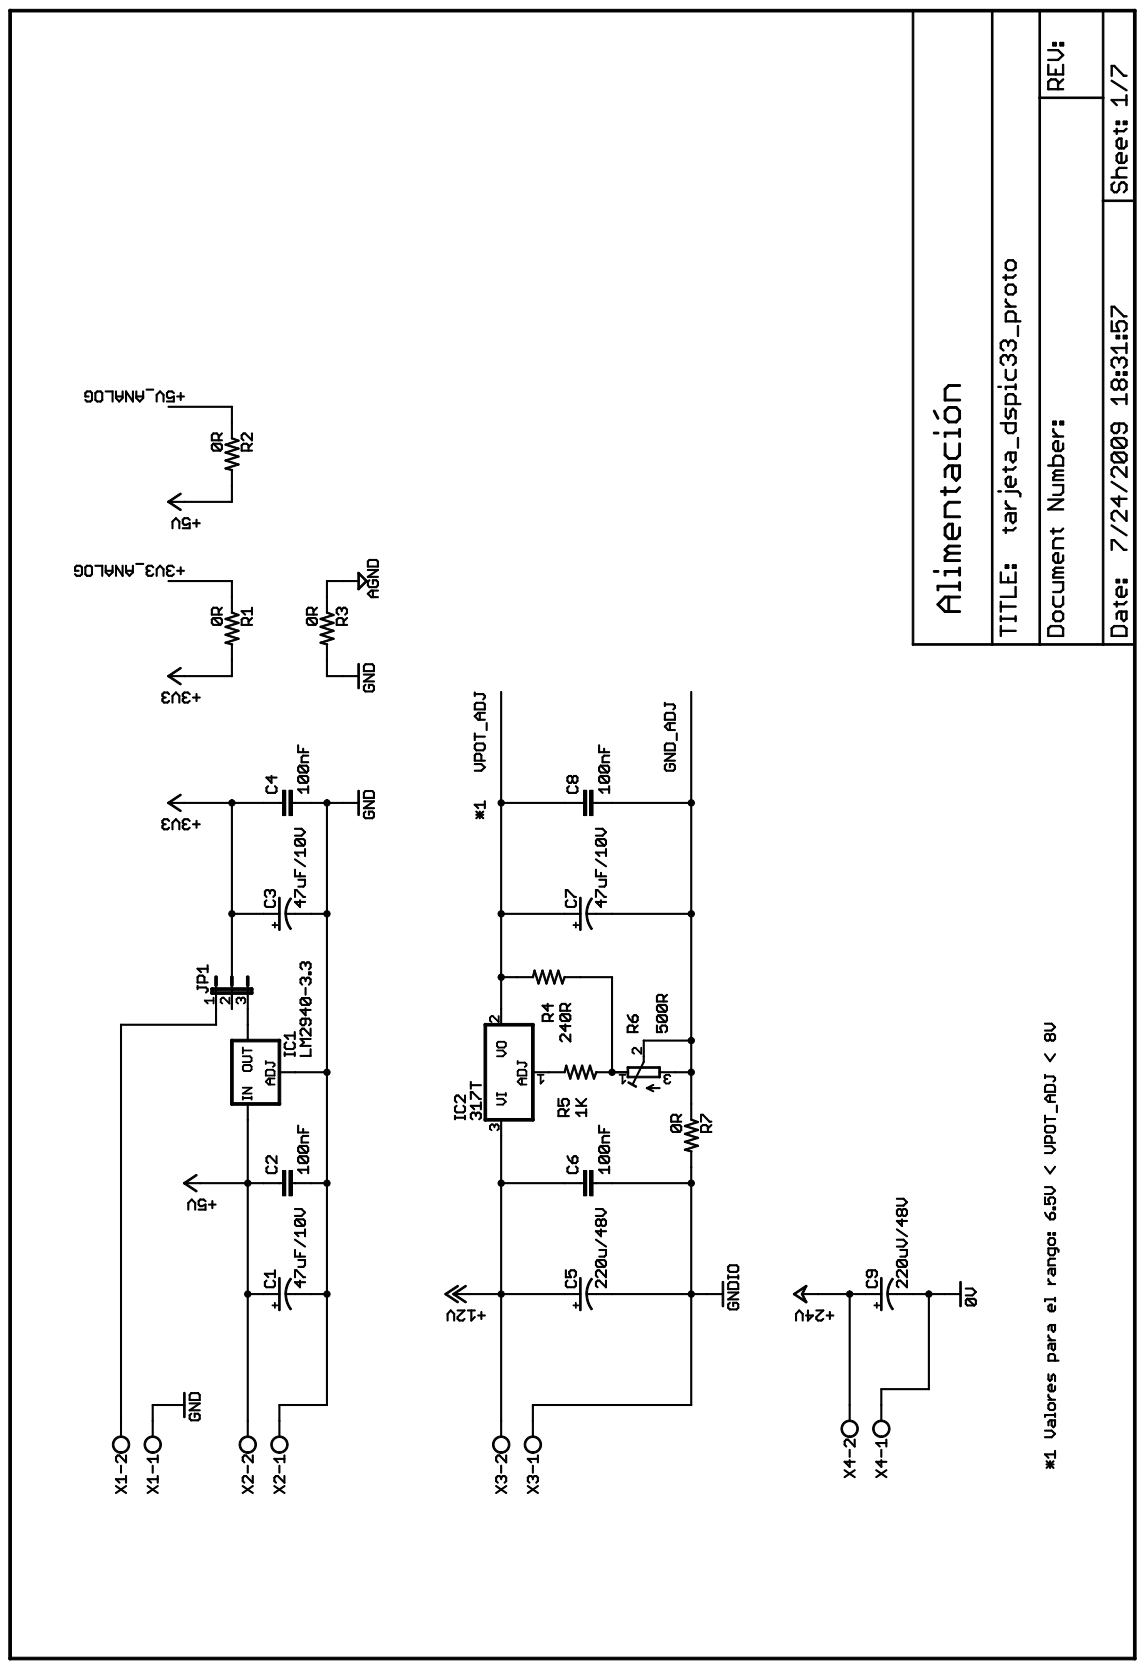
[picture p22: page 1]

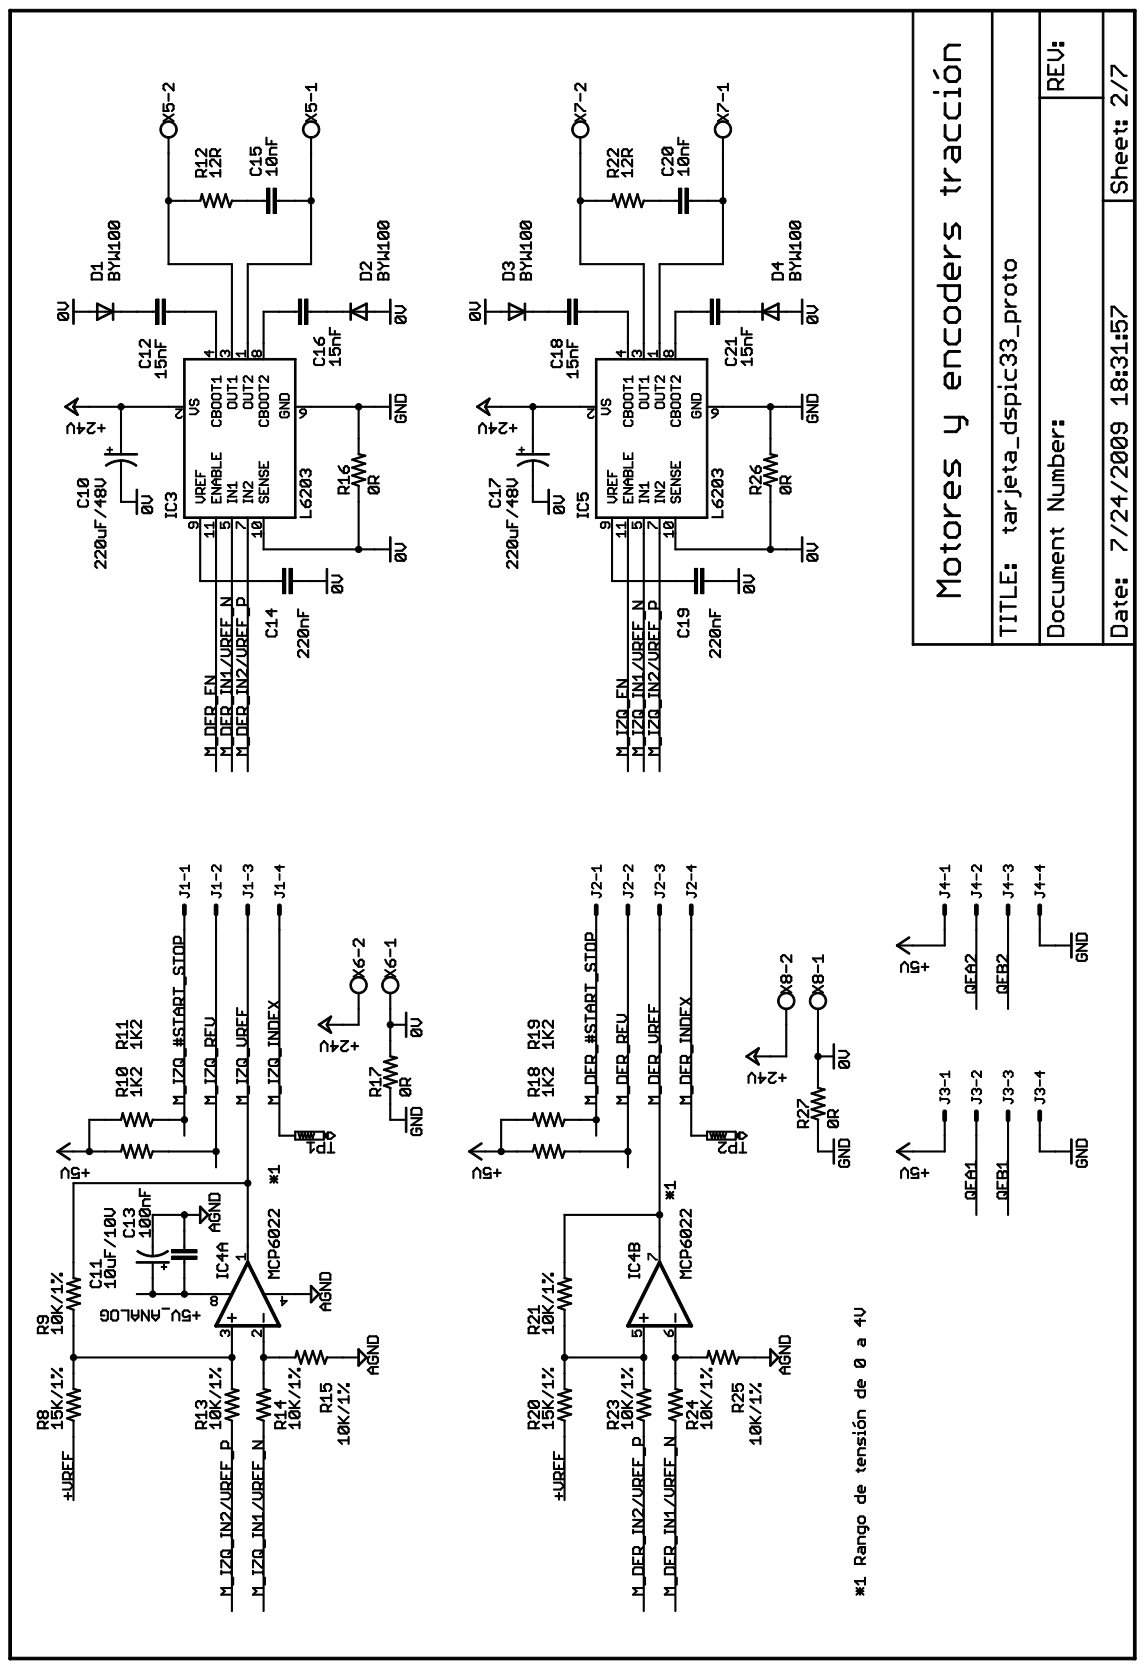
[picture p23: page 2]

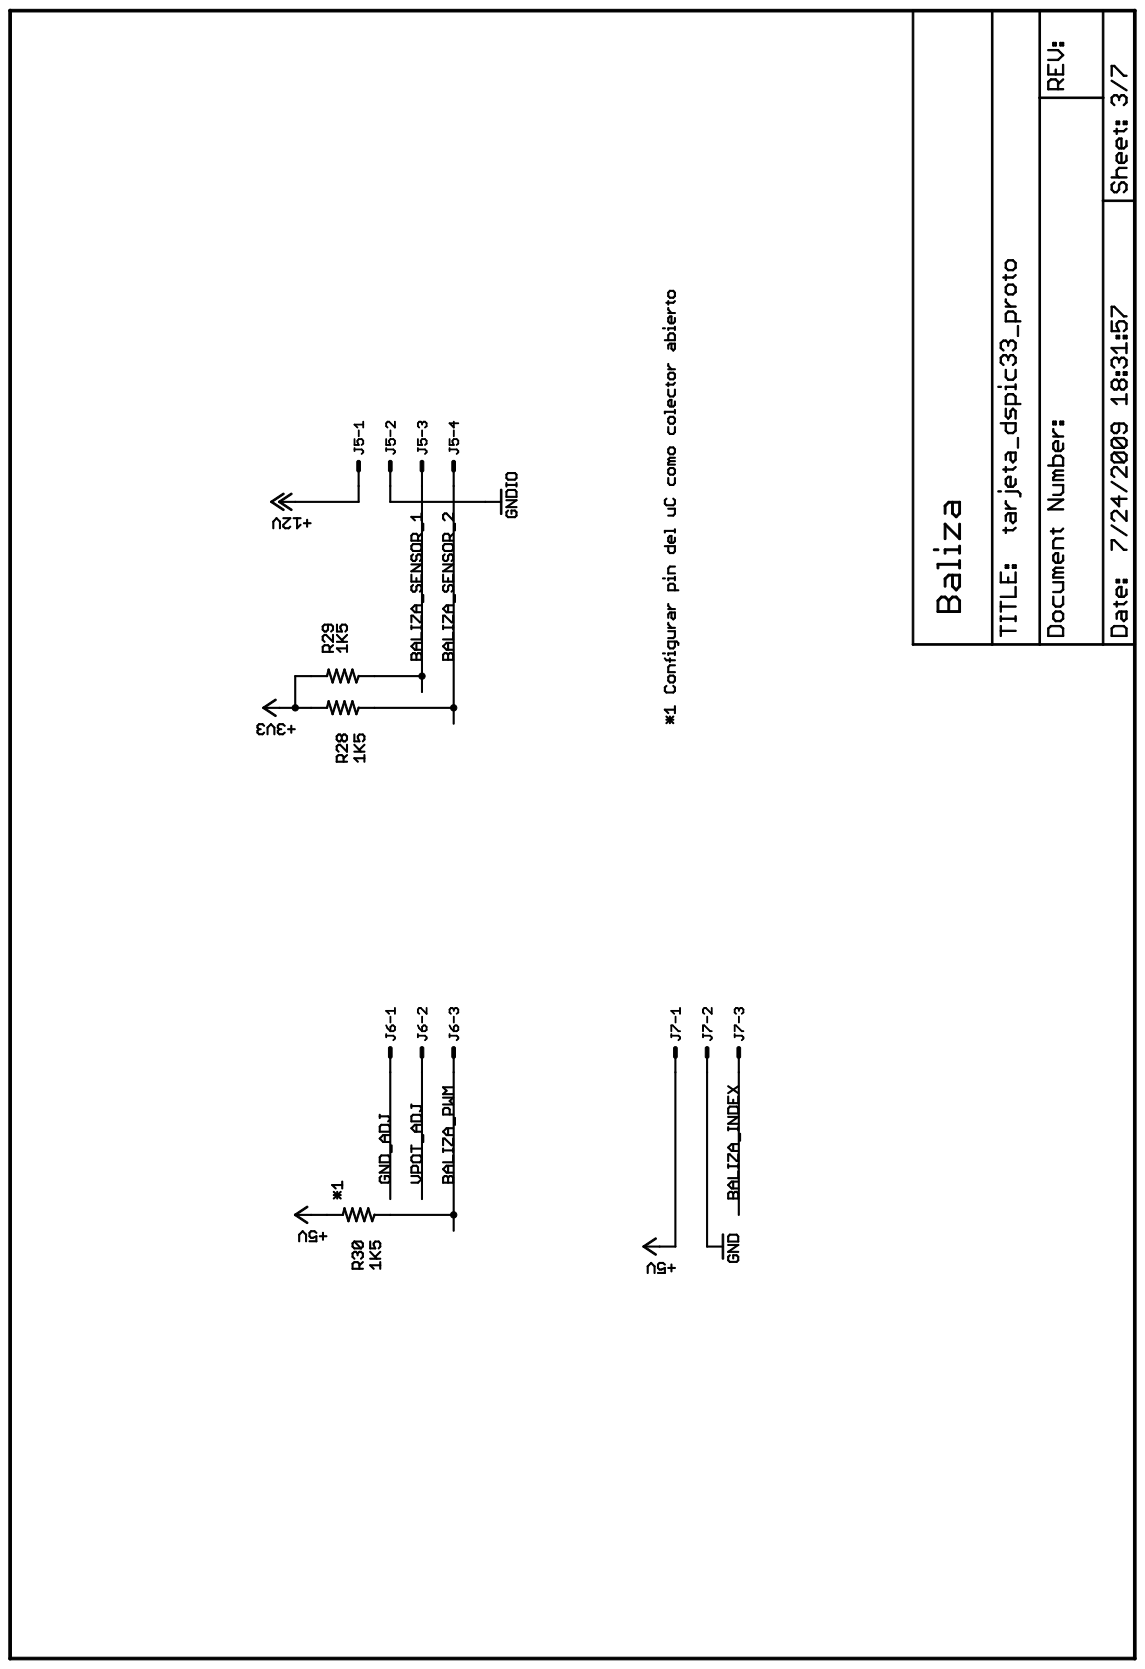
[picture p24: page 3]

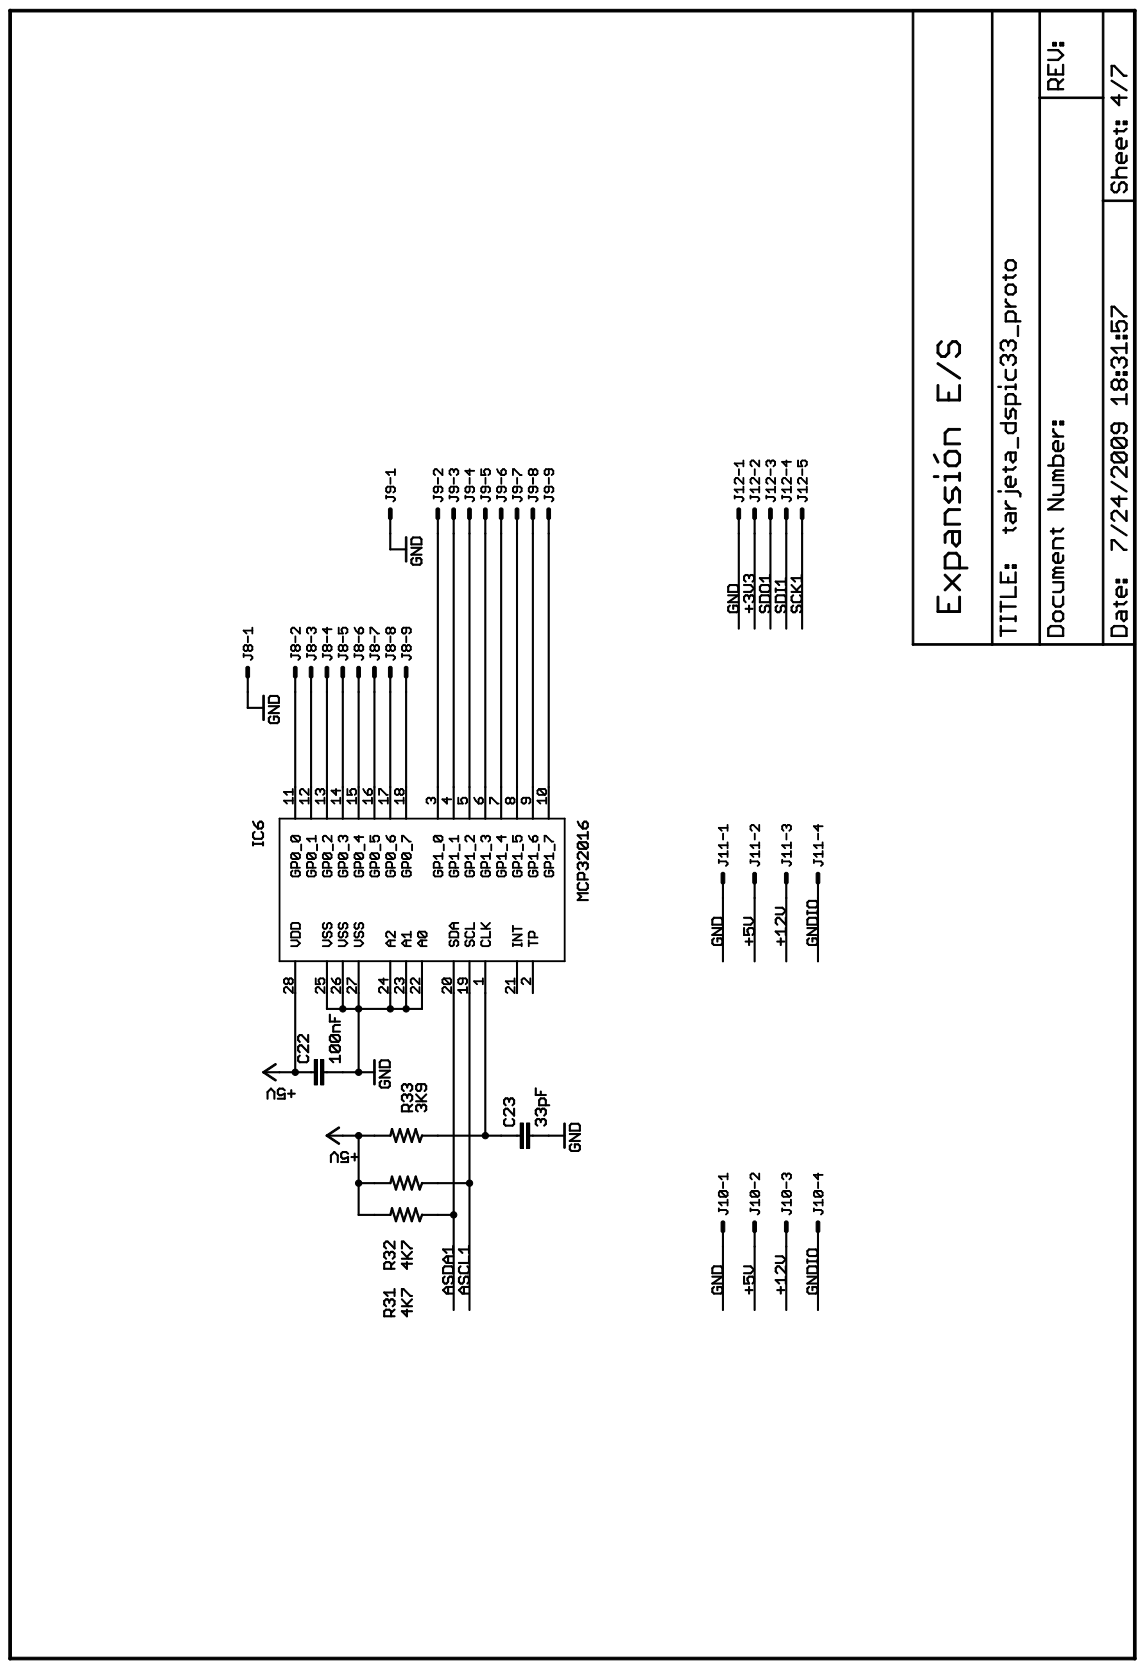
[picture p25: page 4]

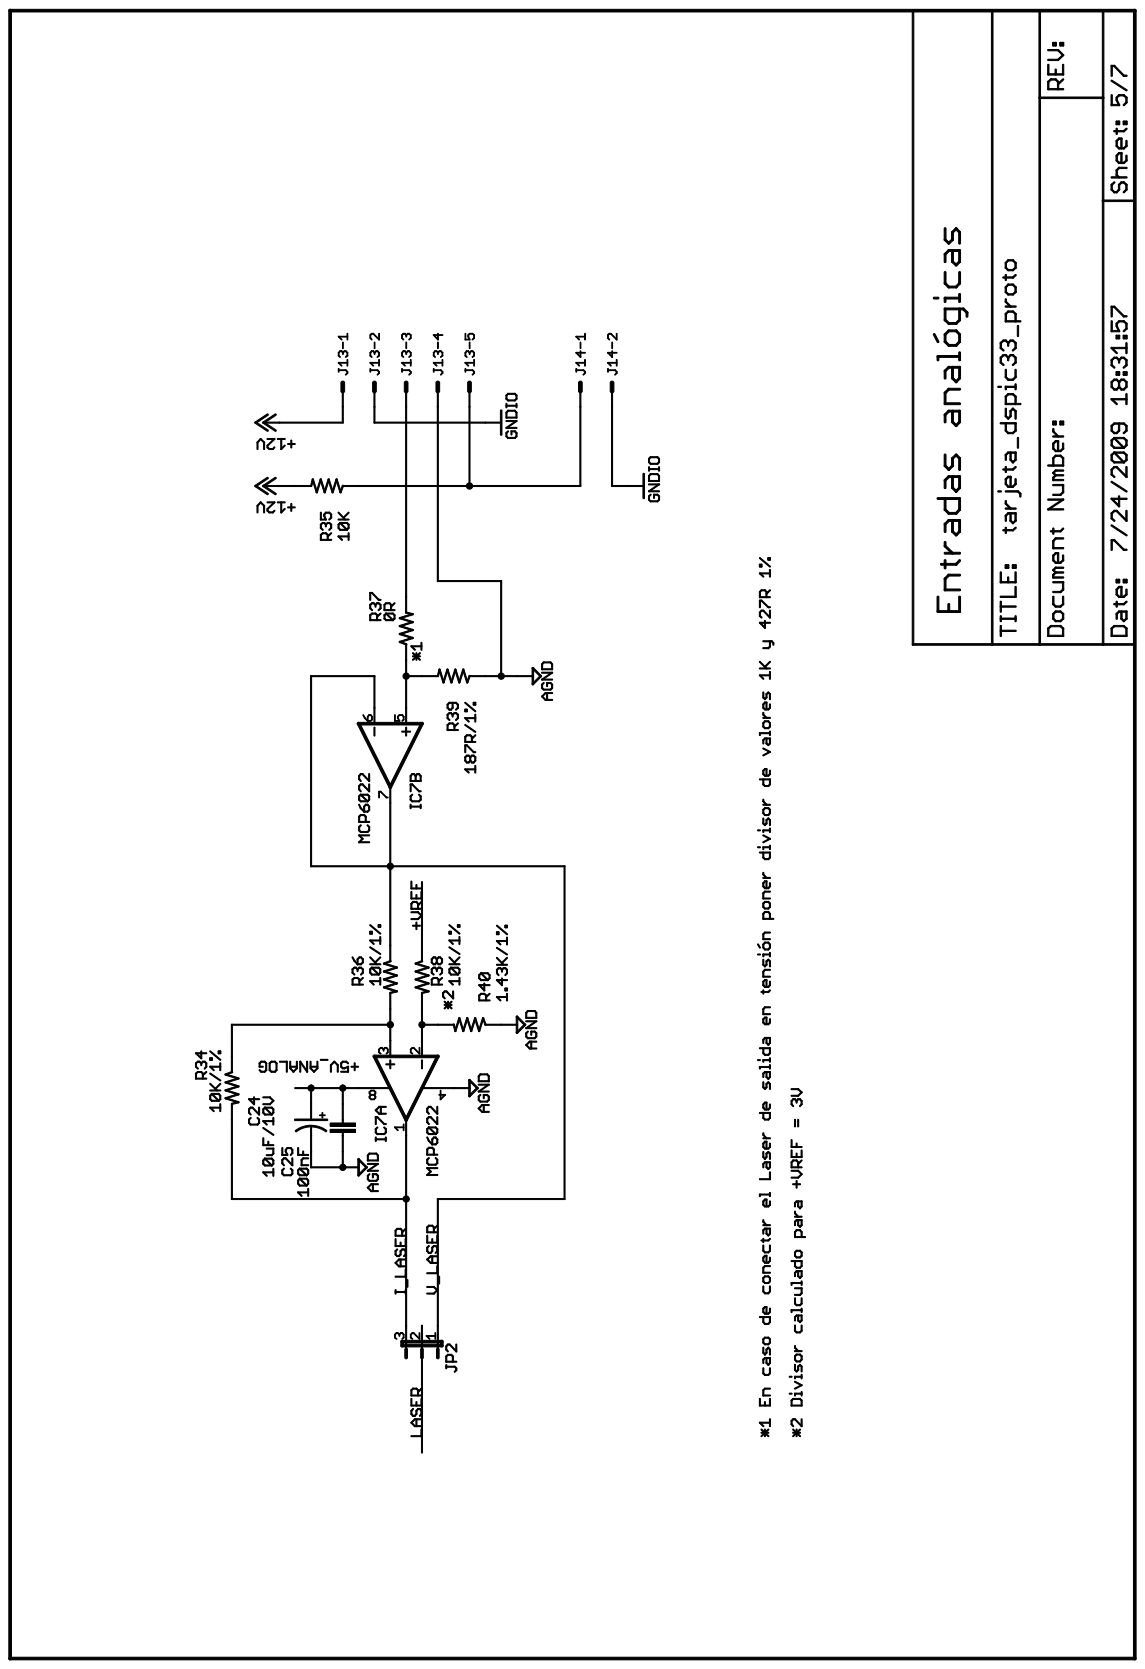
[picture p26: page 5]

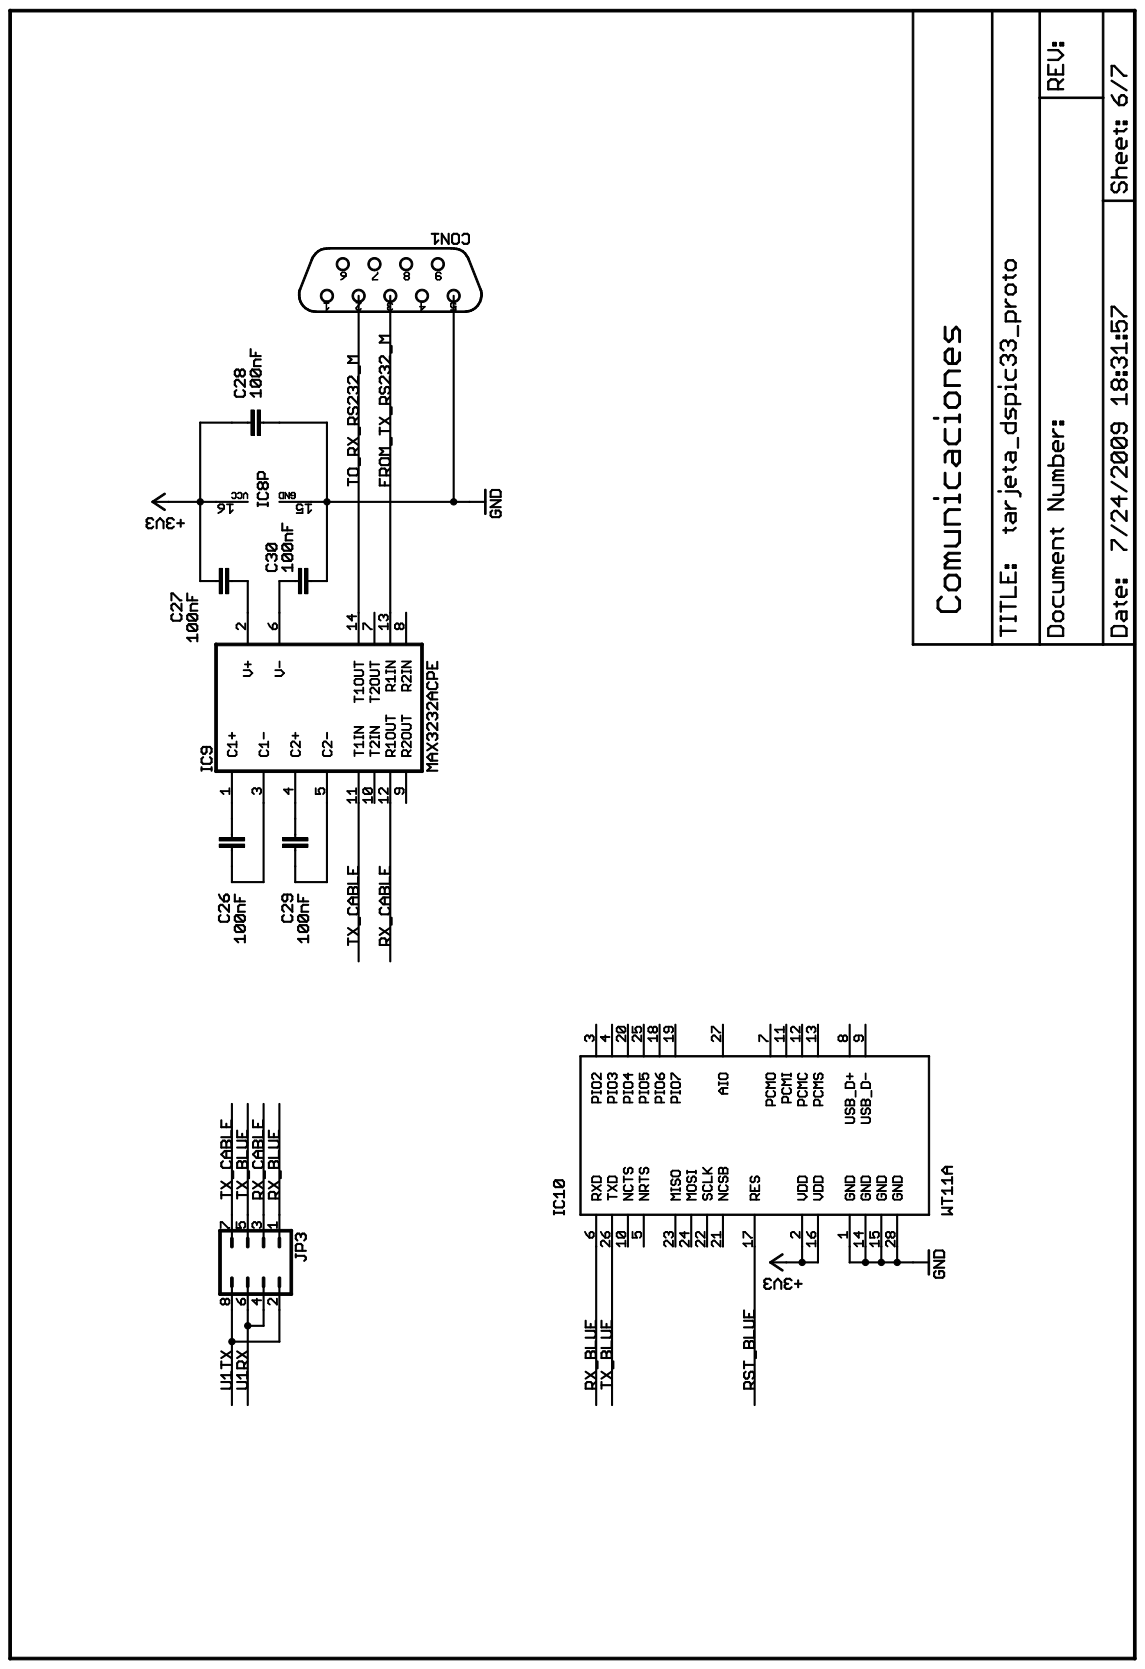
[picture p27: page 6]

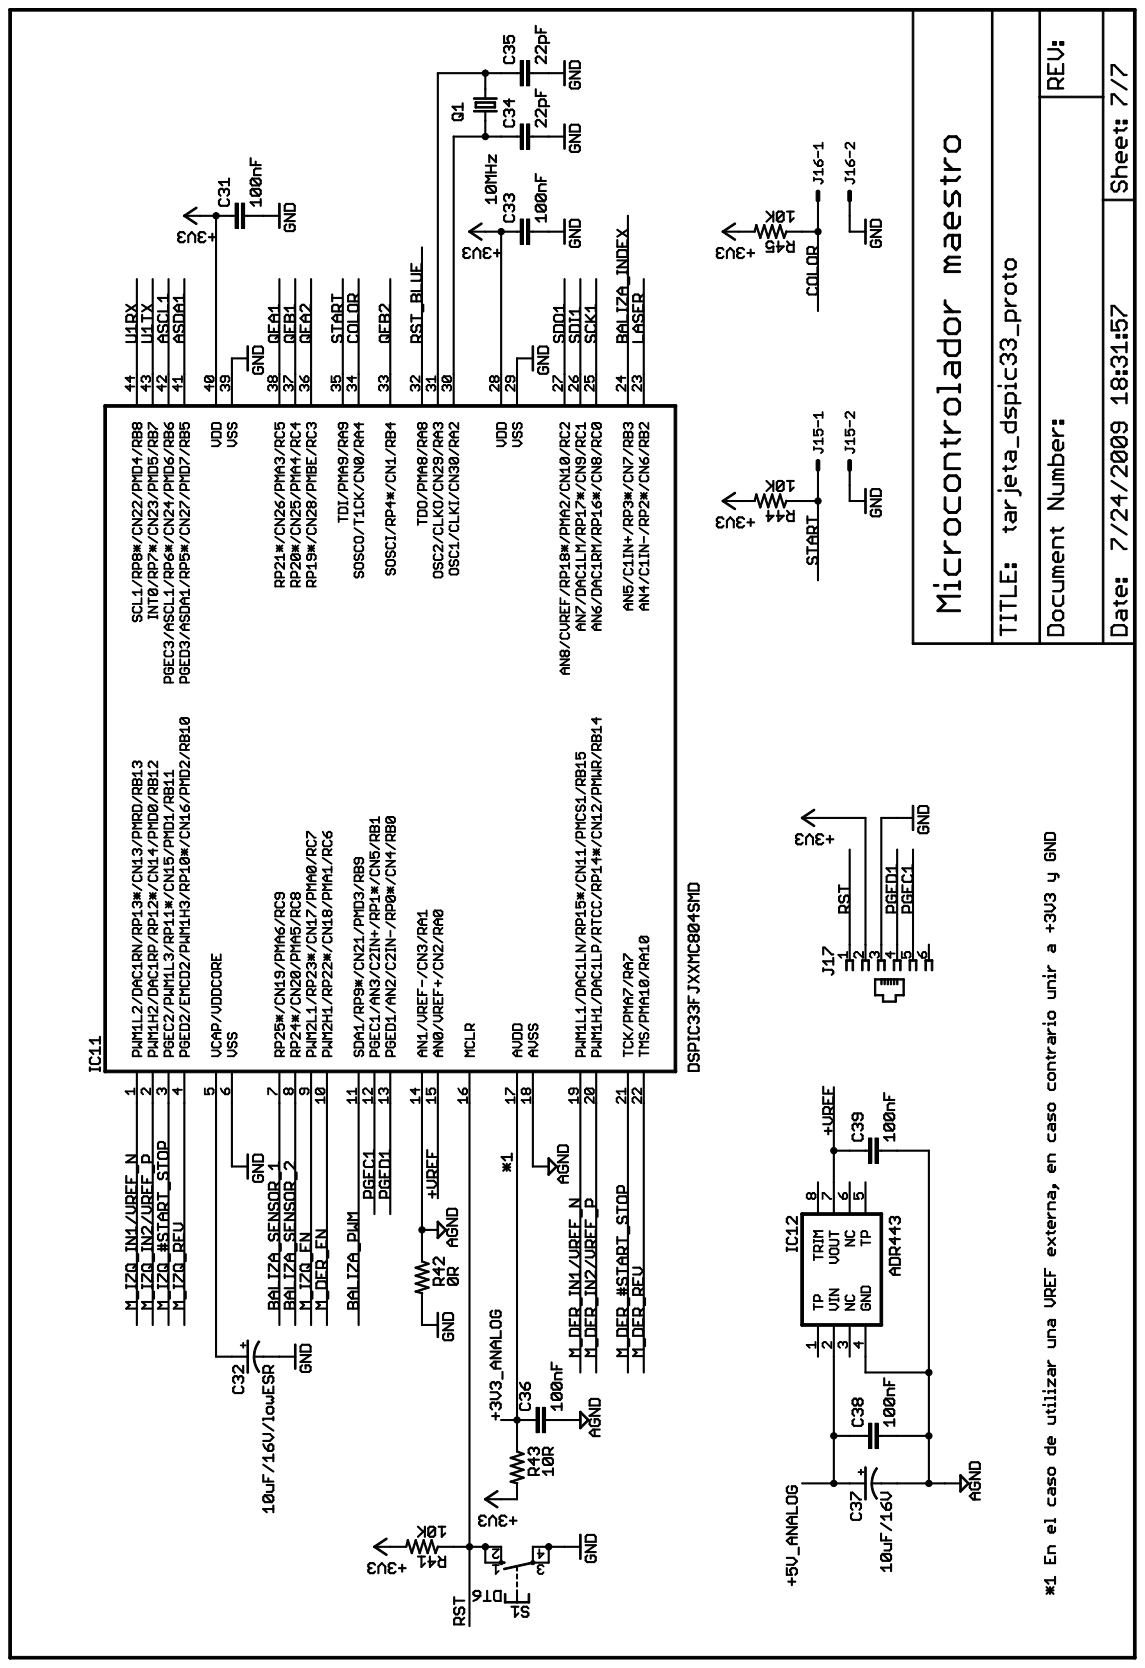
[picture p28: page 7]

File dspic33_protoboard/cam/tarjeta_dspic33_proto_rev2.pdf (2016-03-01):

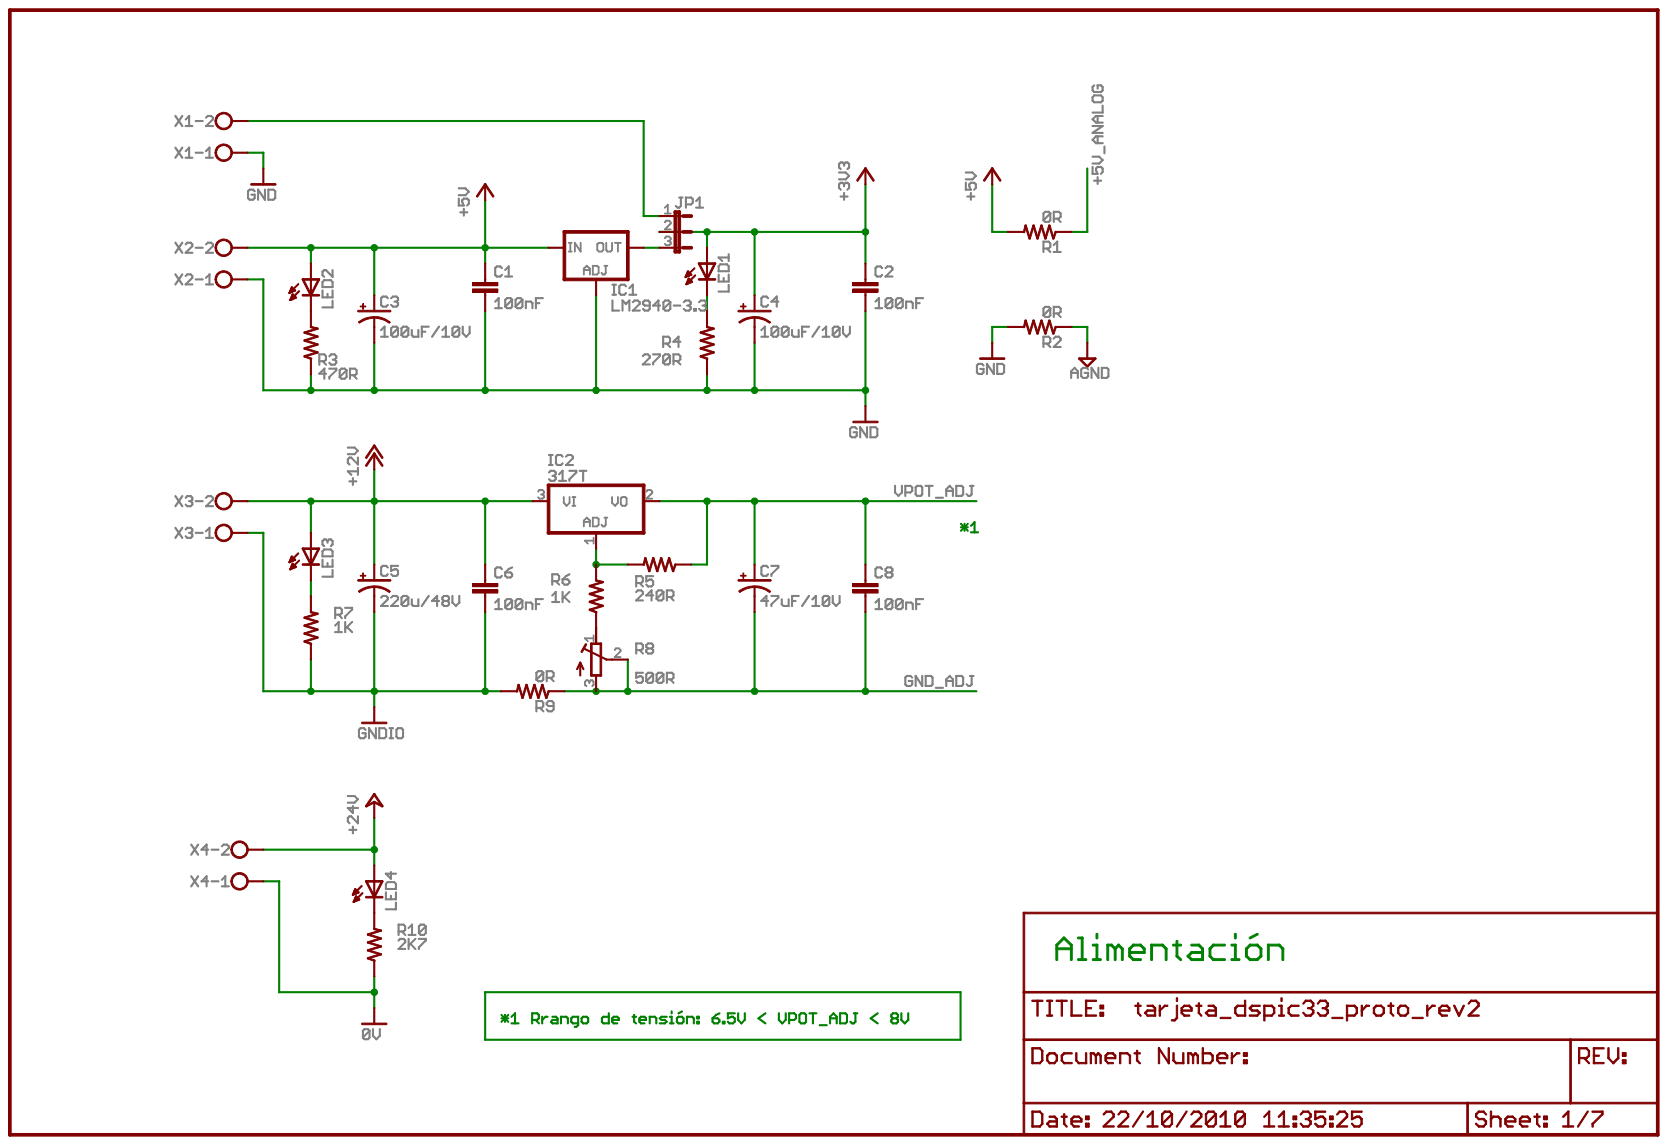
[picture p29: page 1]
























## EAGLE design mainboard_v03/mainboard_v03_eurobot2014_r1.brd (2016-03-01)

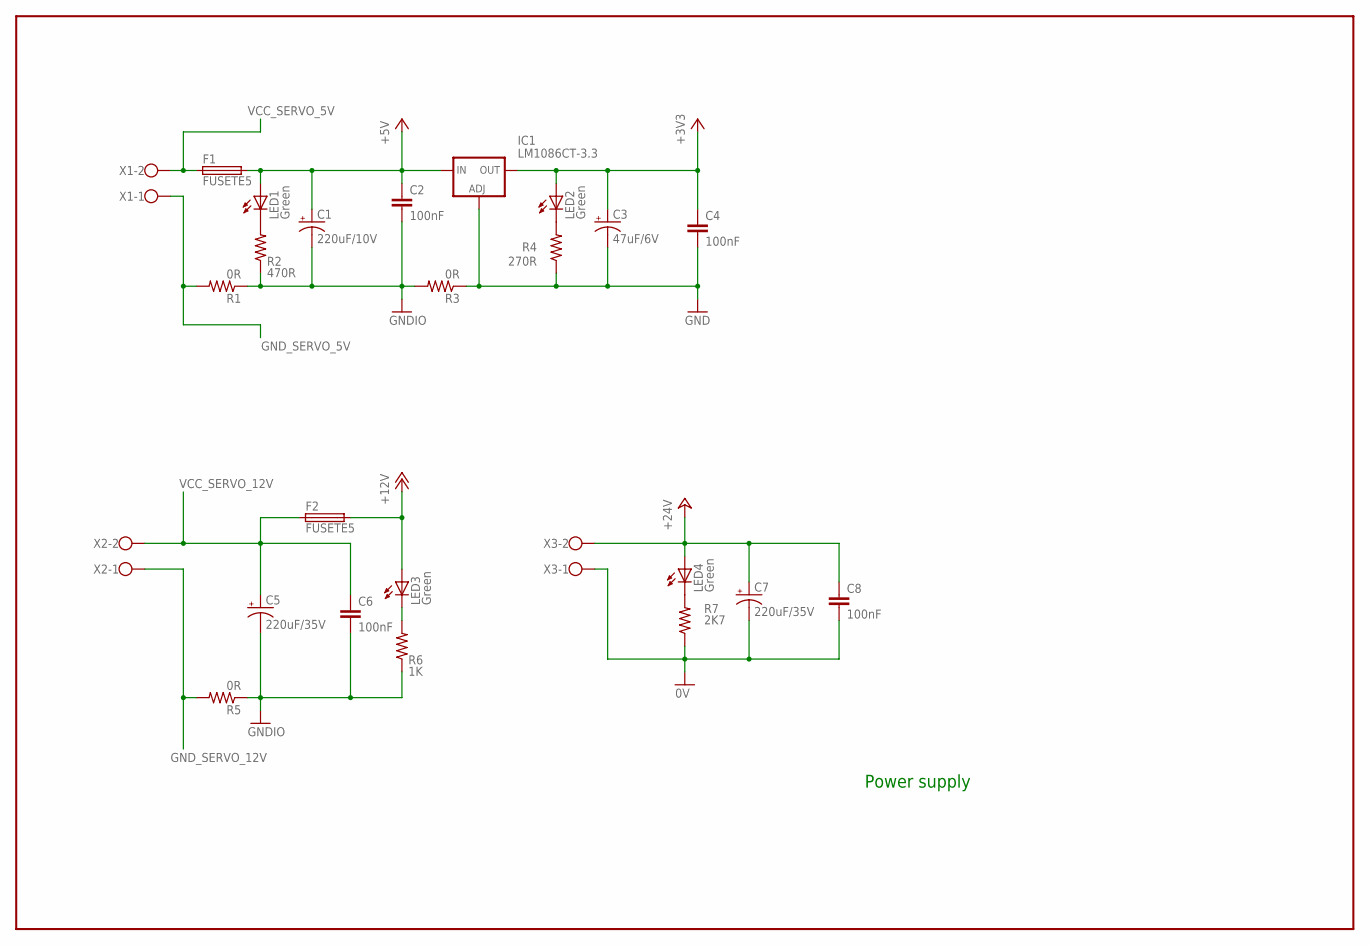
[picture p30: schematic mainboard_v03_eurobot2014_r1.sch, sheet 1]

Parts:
C1: 220uF/10V; E2,5-7
C2, C4, C6, C8: 100nF; C0805
C3: 47uF/6V; SMC_D
C5, C7: 220uF/35V; E5-10,5
F1, F2: FUSETE5; TE5
IC1: LM1086CT-3.3; 317TS
LED1, LED2, LED3, LED4: Green; CHIP-LED0805
R1, R3, R5: 0R; R0805
R2: 470R; R0805
R4: 270R; R0805
R6: 1K; R0805
R7: 2K7; R0805
X1, X2, X3: W237-02P; W237-132

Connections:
0V: C7.-, C8.2, R7.1, X3.1; also elsewhere on the board
+3V3: C3.+, C4.1, IC1.2 (OUT), LED2.A; also elsewhere on the board
+5V: C1.+, C2.1, F1.2, IC1.3 (IN), LED1.A; also elsewhere on the board
+12V: F2.2, LED3.A; also elsewhere on the board
+24V: C7.+, C8.1, LED4.A, X3.2; also elsewhere on the board
GND: C3.-, C4.2, IC1.1 (ADJ), R3.1, R4.1; also elsewhere on the board
GNDIO: C1.-, C2.2, C5.-, C6.2, R1.1, R2.1, R3.2, R5.1, R6.1; also elsewhere on the board
GND_SERVO_5V: R1.2, X1.1; also elsewhere on the board
GND_SERVO_12V: R5.2, X2.1; also elsewhere on the board
unnamed: LED1.C, R2.2
unnamed: LED2.C, R4.2
unnamed: LED3.C, R6.2
unnamed: LED4.C, R7.2
VCC_SERVO_5V: F1.1, X1.2; also elsewhere on the board
VCC_SERVO_12V: C5.+, C6.1, F2.1, X2.2; also elsewhere on the board

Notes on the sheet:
Power supply

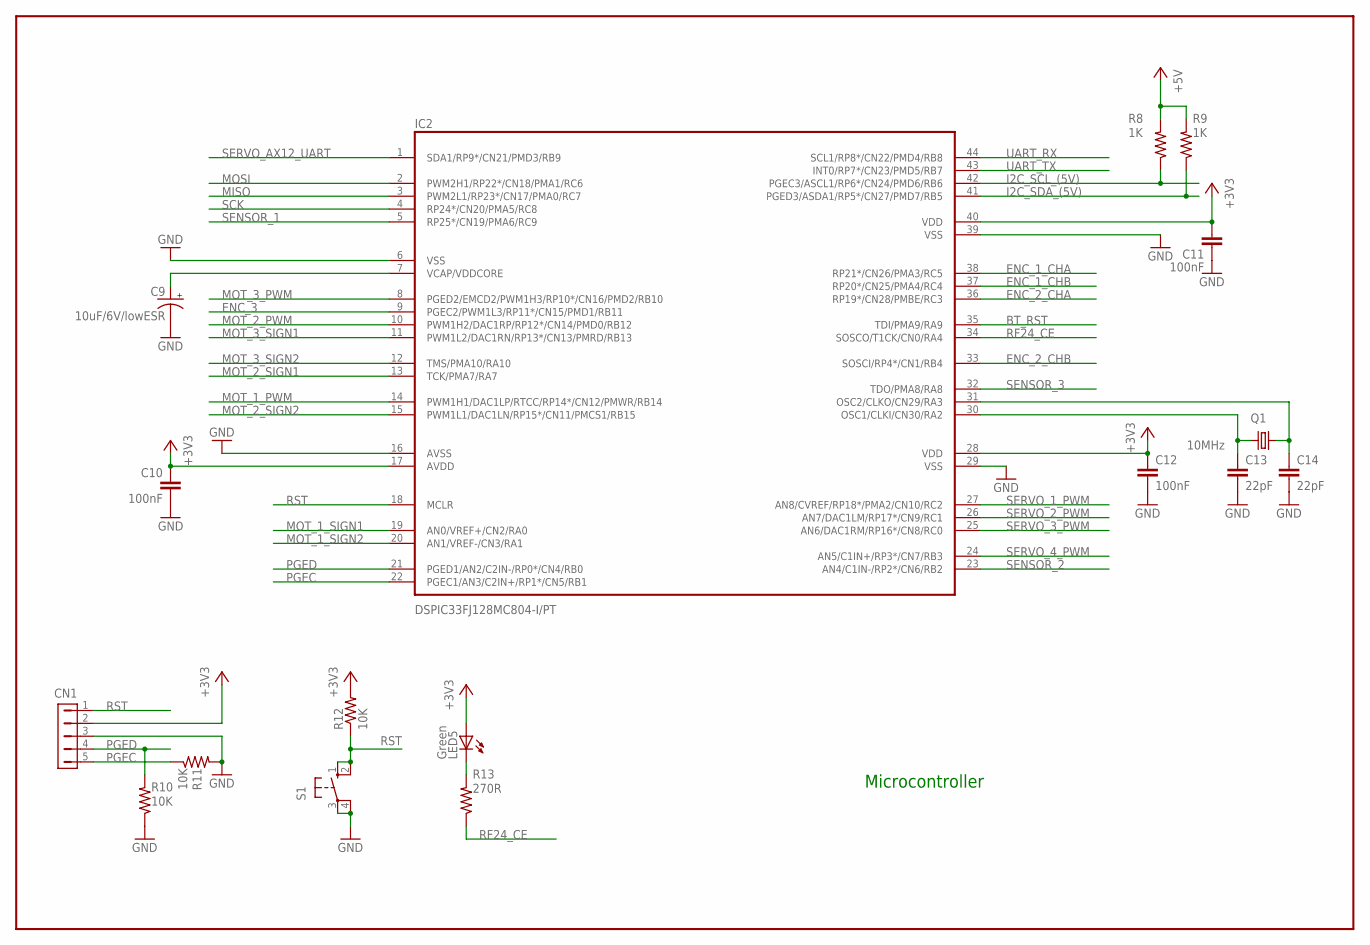
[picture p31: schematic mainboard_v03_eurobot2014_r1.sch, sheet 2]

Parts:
C9: 10uF/6V/lowESR; SMC_A
C10, C11, C12: 100nF; C0603
C13, C14: 22pF; C0805
CN1: HDR-1X5-SIP-100; SIP-100-5V
IC2: DSPIC33FJ128MC804-I/PT; TQFP44
LED5: Green; CHIP-LED0805
Q1: 10MHz; HC49UP
R8, R9: 1K; R0805
R10, R11, R12: 10K; R0805
R13: 270R; R0805
S1: 10-XX; B3F-10XX

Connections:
+3V3: C10.1, C11.1, C12.1, CN1.2, IC2.17 (AVDD), IC2.28 (VDD), IC2.40 (VDD), LED5.A, R12.2; also elsewhere on the board
+5V: R8.2, R9.2; also elsewhere on the board
BT_RST: IC2.35 (TDI/PMA9/RA9); also elsewhere on the board
ENC_1_CHA: IC2.38 (RP21*/CN26/PMA3/RC5); also elsewhere on the board
ENC_1_CHB: IC2.37 (RP20*/CN25/PMA4/RC4); also elsewhere on the board
ENC_2_CHA: IC2.36 (RP19*/CN28/PMBE/RC3); also elsewhere on the board
ENC_2_CHB: IC2.33 (SOSCI/RP4*/CN1/RB4); also elsewhere on the board
ENC_3: IC2.9 (PGEC2/PWM1L3/RP11*/CN15/PMD1/RB11); also elsewhere on the board
GND: C9.-, C10.2, C11.2, C12.2, C13.2, C14.2, CN1.3, IC2.6 (VSS), IC2.16 (AVSS), IC2.29 (VSS), IC2.39 (VSS), R10.1, R11.2, S1.3, S1.4 (P1); also elsewhere on the board
I2C_SCL_(5V): IC2.42 (PGEC3/ASCL1/RP6*/CN24/PMD6/RB6), R8.1; also elsewhere on the board
I2C_SDA_(5V): IC2.41 (PGED3/ASDA1/RP5*/CN27/PMD7/RB5), R9.1; also elsewhere on the board
MISO: IC2.3 (PWM2L1/RP23*/CN17/PMA0/RC7); also elsewhere on the board
MOSI: IC2.2 (PWM2H1/RP22*/CN18/PMA1/RC6); also elsewhere on the board
MOT_1_PWM: IC2.14 (PWM1H1/DAC1LP/RTCC/RP14*/CN12/PMWR/RB14); also elsewhere on the board
MOT_1_SIGN1: IC2.19 (AN0/VREF+/CN2/RA0); also elsewhere on the board
MOT_1_SIGN2: IC2.20 (AN1/VREF-/CN3/RA1); also elsewhere on the board
MOT_2_PWM: IC2.10 (PWM1H2/DAC1RP/RP12*/CN14/PMD0/RB12); also elsewhere on the board
MOT_2_SIGN1: IC2.13 (TCK/PMA7/RA7); also elsewhere on the board
MOT_2_SIGN2: IC2.15 (PWM1L1/DAC1LN/RP15*/CN11/PMCS1/RB15); also elsewhere on the board
MOT_3_PWM: IC2.8 (PGED2/EMCD2/PWM1H3/RP10*/CN16/PMD2/RB10); also elsewhere on the board
MOT_3_SIGN1: IC2.11 (PWM1L2/DAC1RN/RP13*/CN13/PMRD/RB13); also elsewhere on the board
MOT_3_SIGN2: IC2.12 (TMS/PMA10/RA10); also elsewhere on the board
unnamed: LED5.C, R13.2
unnamed: C14.1, IC2.31 (OSC2/CLKO/CN29/RA3), Q1.2
unnamed: C13.1, IC2.30 (OSC1/CLKI/CN30/RA2), Q1.1
unnamed: C9.+, IC2.7 (VCAP/VDDCORE)
PGEC: CN1.5, IC2.22 (PGEC1/AN3/C2IN+/RP1*/CN5/RB1), R11.1
PGED: CN1.4, IC2.21 (PGED1/AN2/C2IN-/RP0*/CN4/RB0), R10.2
RF24_CE: IC2.34 (SOSCO/T1CK/CN0/RA4), R13.1; also elsewhere on the board
RST: CN1.1, IC2.18 (MCLR), R12.1, S1.1 (S), S1.2 (S1)
SCK: IC2.4 (RP24*/CN20/PMA5/RC8); also elsewhere on the board
SENSOR_1: IC2.5 (RP25*/CN19/PMA6/RC9); also elsewhere on the board
SENSOR_2: IC2.23 (AN4/C1IN-/RP2*/CN6/RB2); also elsewhere on the board
SENSOR_3: IC2.32 (TDO/PMA8/RA8); also elsewhere on the board
SERVO_1_PWM: IC2.27 (AN8/CVREF/RP18*/PMA2/CN10/RC2); also elsewhere on the board
SERVO_2_PWM: IC2.26 (AN7/DAC1LM/RP17*/CN9/RC1); also elsewhere on the board
SERVO_3_PWM: IC2.25 (AN6/DAC1RM/RP16*/CN8/RC0); also elsewhere on the board
SERVO_4_PWM: IC2.24 (AN5/C1IN+/RP3*/CN7/RB3); also elsewhere on the board
SERVO_AX12_UART: IC2.1 (SDA1/RP9*/CN21/PMD3/RB9); also elsewhere on the board
UART_RX: IC2.44 (SCL1/RP8*/CN22/PMD4/RB8); also elsewhere on the board
UART_TX: IC2.43 (INT0/RP7*/CN23/PMD5/RB7); also elsewhere on the board

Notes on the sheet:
Microcontroller

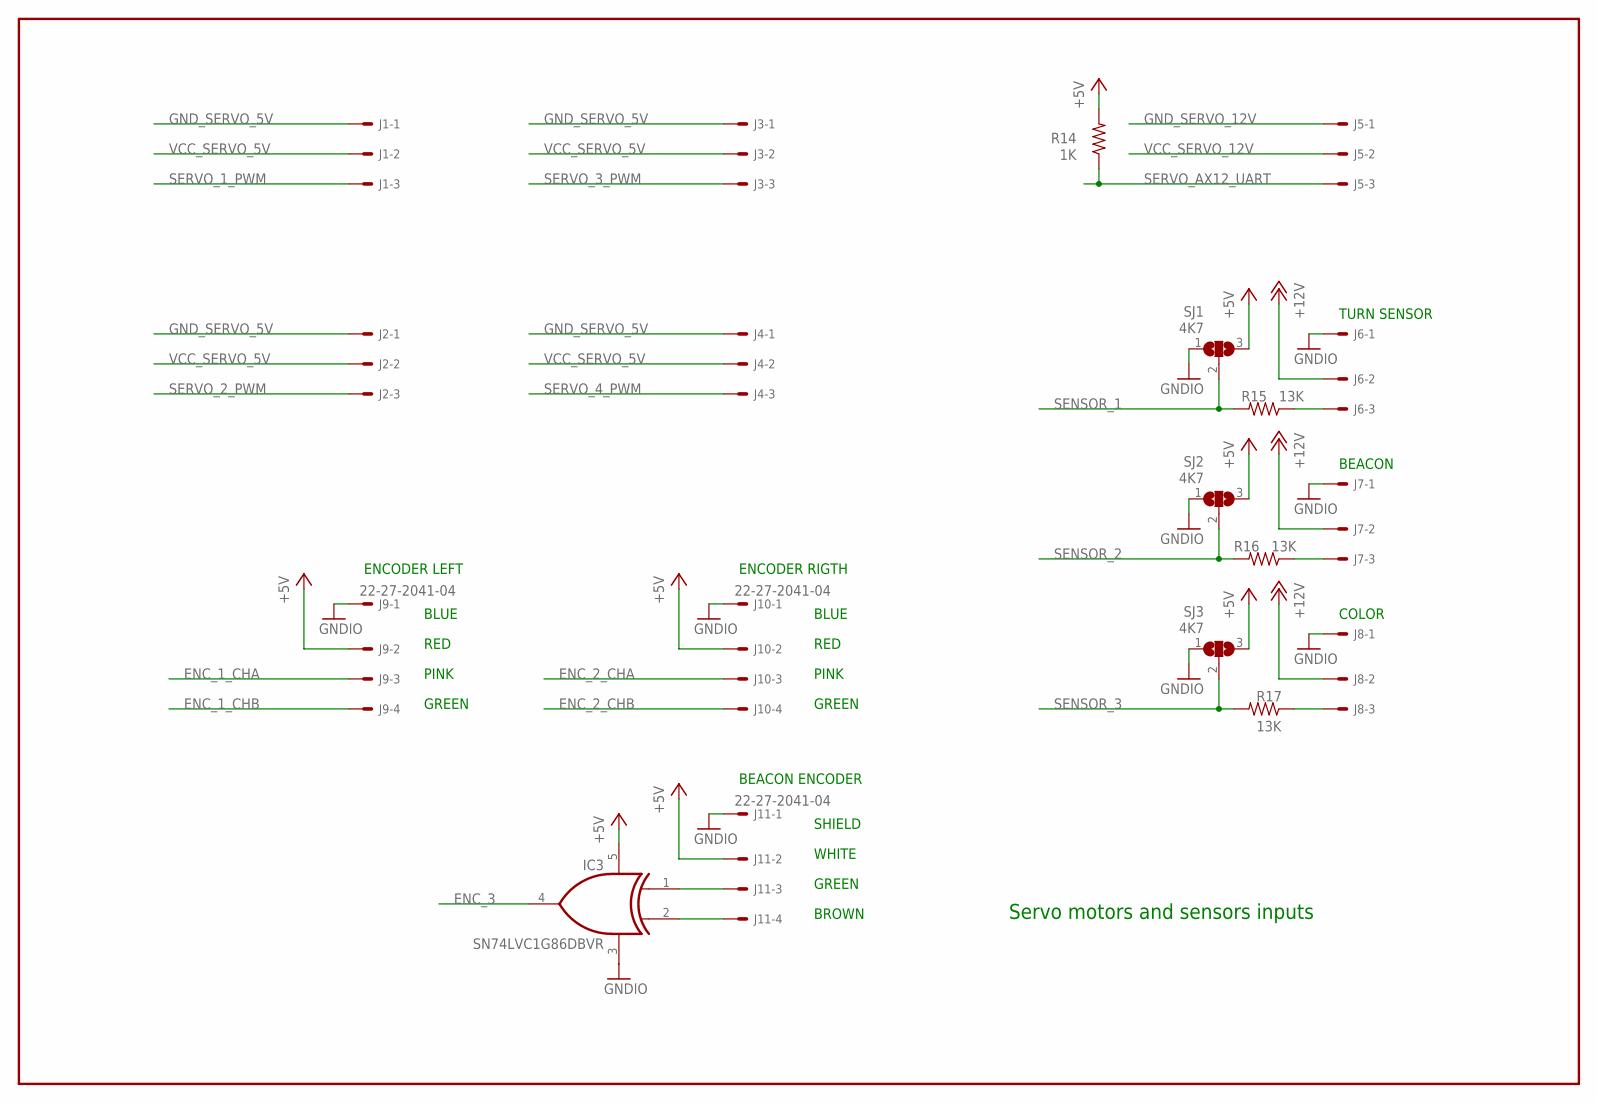
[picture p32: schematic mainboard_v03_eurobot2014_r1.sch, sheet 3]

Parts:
IC3: SN74LVC1G86DBVR; SOT23-5
J1, J2, J3, J4, J5, J6, J7, J8: 22-27-2031-03; 6410-03
J9, J10, J11: 22-27-2041-04; 6410-04
R14: 1K; R0805
R15, R16, R17: 13K; R0805
SJ1, SJ2, SJ3: 4K7; SJ_2

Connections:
+5V: IC3.5 (VCC), J9.2, J10.2, J11.2, R14.2, SJ1.3, SJ2.3, SJ3.3; also elsewhere on the board
+12V: J6.2, J7.2, J8.2; also elsewhere on the board
ENC_1_CHA: J9.3; also elsewhere on the board
ENC_1_CHB: J9.4; also elsewhere on the board
ENC_2_CHA: J10.3; also elsewhere on the board
ENC_2_CHB: J10.4; also elsewhere on the board
ENC_3: IC3.4 (O); also elsewhere on the board
GNDIO: IC3.3 (GND), J6.1, J7.1, J8.1, J9.1, J10.1, J11.1, SJ1.1, SJ2.1, SJ3.1; also elsewhere on the board
GND_SERVO_5V: J1.1, J2.1, J3.1, J4.1; also elsewhere on the board
GND_SERVO_12V: J5.1; also elsewhere on the board
unnamed: J6.3, R15.1
unnamed: IC3.1 (I0), J11.3
unnamed: IC3.2 (I1), J11.4
unnamed: J7.3, R16.1
unnamed: J8.3, R17.1
SENSOR_1: R15.2, SJ1.2; also elsewhere on the board
SENSOR_2: R16.2, SJ2.2; also elsewhere on the board
SENSOR_3: R17.2, SJ3.2; also elsewhere on the board
SERVO_1_PWM: J1.3; also elsewhere on the board
SERVO_2_PWM: J2.3; also elsewhere on the board
SERVO_3_PWM: J3.3; also elsewhere on the board
SERVO_4_PWM: J4.3; also elsewhere on the board
SERVO_AX12_UART: J5.3, R14.1; also elsewhere on the board
VCC_SERVO_5V: J1.2, J2.2, J3.2, J4.2; also elsewhere on the board
VCC_SERVO_12V: J5.2; also elsewhere on the board

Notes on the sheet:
Servo motors and sensors inputs
WHITE
GREEN
BROWN
SHIELD
BEACON ENCODER
ENCODER LEFT
ENCODER RIGTH
PINK
RED
BLUE
BEACON
TURN SENSOR
COLOR

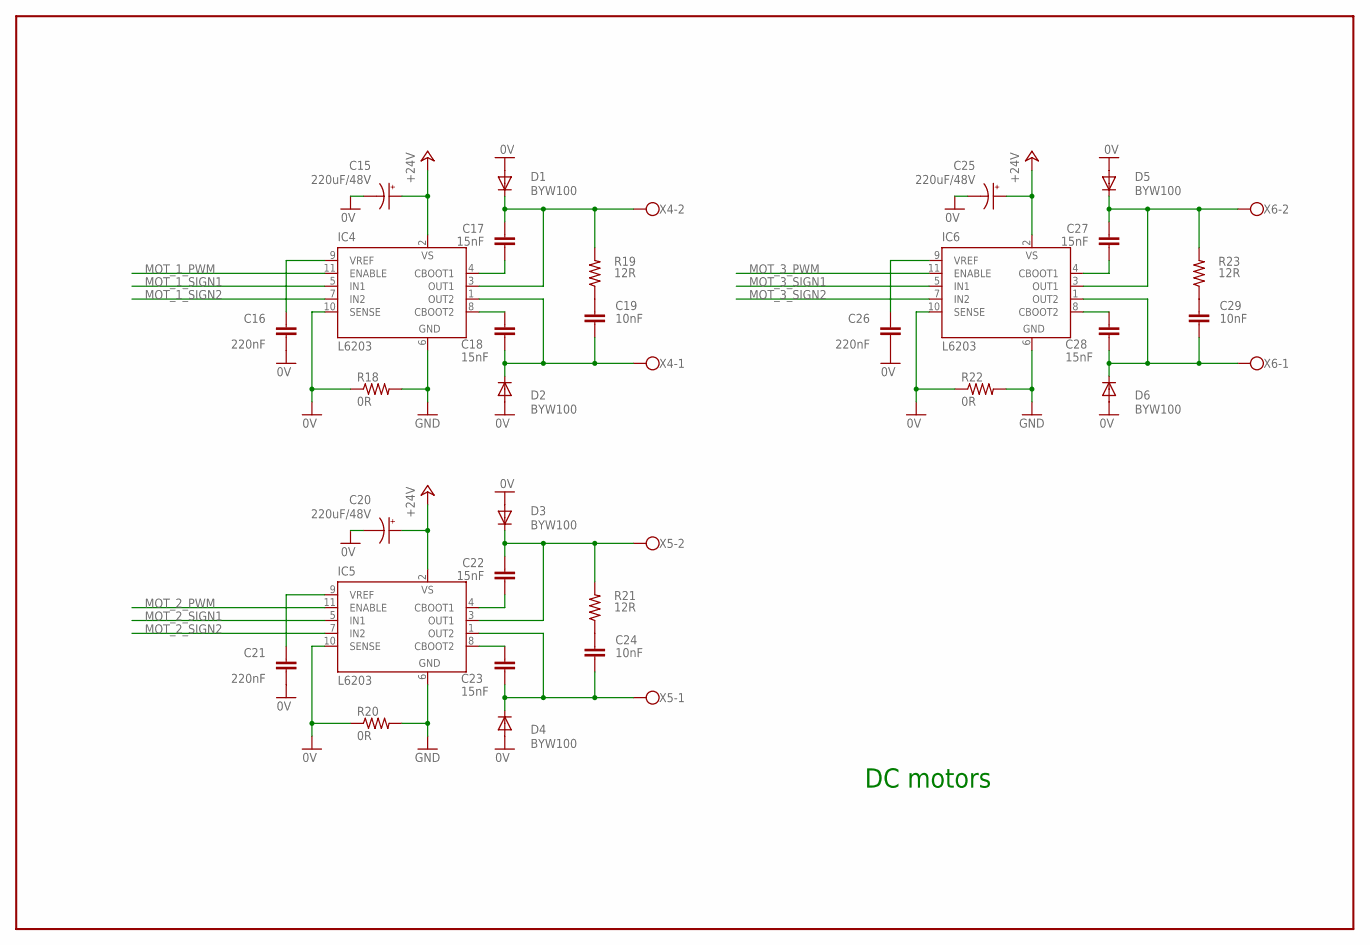
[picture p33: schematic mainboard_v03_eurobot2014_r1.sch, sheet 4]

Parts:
C15, C20, C25: 220uF/48V; E3,5-10
C16, C21, C26: 220nF; C0805
C17, C18, C22, C23, C27, C28: 15nF; C0805
C19, C24, C29: 10nF; C0805
D1, D2, D3, D4, D5, D6: BYW100; F126-10
IC4, IC5, IC6: L6203; MULTIWATT-11
R18, R20, R22: 0R; M0805
R19, R21, R23: 12R; M0805
X4, X5, X6: W237-02P; W237-132

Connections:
0V: C15.-, C16.2, C20.-, C21.2, C25.-, C26.2, D1.A, D2.A, D3.A, D4.A, D5.A, D6.A, IC4.10 (SENSE), IC5.10 (SENSE), IC6.10 (SENSE), R18.1, R20.1, R22.1; also elsewhere on the board
+24V: C15.+, C20.+, C25.+, IC4.2 (VS), IC5.2 (VS), IC6.2 (VS); also elsewhere on the board
GND: IC4.6 (GND), IC5.6 (GND), IC6.6 (GND), R18.2, R20.2, R22.2; also elsewhere on the board
MOT_1_PWM: IC4.11 (ENABLE); also elsewhere on the board
MOT_1_SIGN1: IC4.5 (IN1); also elsewhere on the board
MOT_1_SIGN2: IC4.7 (IN2); also elsewhere on the board
MOT_2_PWM: IC5.11 (ENABLE); also elsewhere on the board
MOT_2_SIGN1: IC5.5 (IN1); also elsewhere on the board
MOT_2_SIGN2: IC5.7 (IN2); also elsewhere on the board
MOT_3_PWM: IC6.11 (ENABLE); also elsewhere on the board
MOT_3_SIGN1: IC6.5 (IN1); also elsewhere on the board
MOT_3_SIGN2: IC6.7 (IN2); also elsewhere on the board
unnamed: C16.1, IC4.9 (VREF)
unnamed: C18.1, IC4.8 (CBOOT2)
unnamed: C17.1, IC4.4 (CBOOT1)
unnamed: C19.2, R19.1
unnamed: C17.2, D1.C, IC4.3 (OUT1), R19.2, X4.2
unnamed: C18.2, C19.1, D2.C, IC4.1 (OUT2), X4.1
unnamed: C21.1, IC5.9 (VREF)
unnamed: C26.1, IC6.9 (VREF)
unnamed: C28.1, IC6.8 (CBOOT2)
unnamed: C27.1, IC6.4 (CBOOT1)
unnamed: C23.1, IC5.8 (CBOOT2)
unnamed: C29.2, R23.1
unnamed: C22.1, IC5.4 (CBOOT1)
unnamed: C24.2, R21.1
unnamed: C22.2, D3.C, IC5.3 (OUT1), R21.2, X5.2
unnamed: C23.2, C24.1, D4.C, IC5.1 (OUT2), X5.1
unnamed: C27.2, D5.C, IC6.3 (OUT1), R23.2, X6.2
unnamed: C28.2, C29.1, D6.C, IC6.1 (OUT2), X6.1

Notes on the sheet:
DC motors

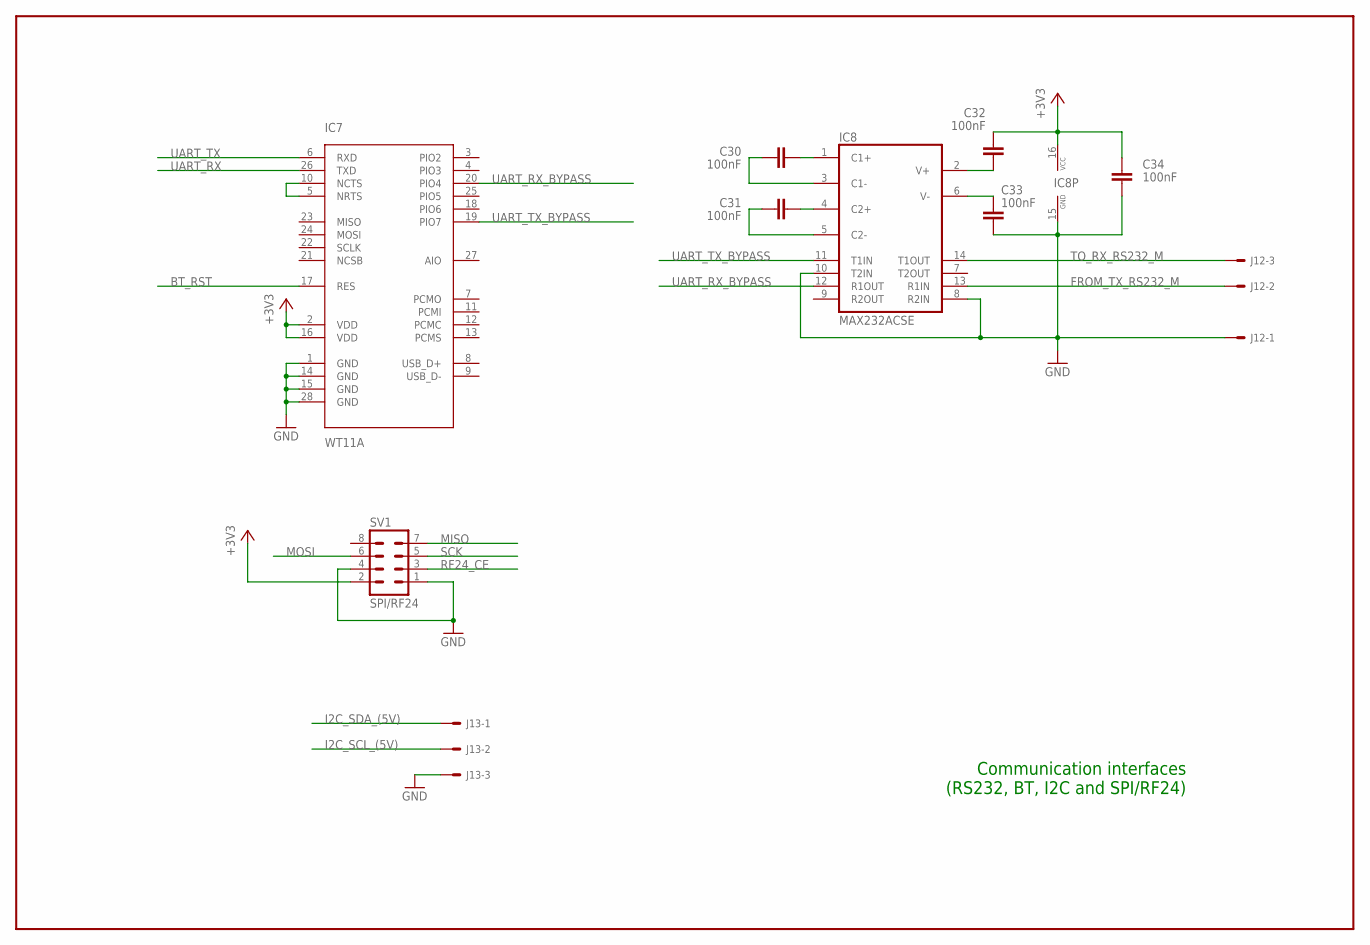
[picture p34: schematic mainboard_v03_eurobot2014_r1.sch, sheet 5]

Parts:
C30, C31, C32, C33, C34: 100nF; C0603
IC7: WT11A; WT11
IC8: MAX232ACSE; SO16
J12, J13: 22-27-2031-03; 6410-03
SV1: SPI/RF24; MA04-2

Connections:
+3V3: C32.2, C34.2, IC7.2 (VDD), IC7.16 (VDD), IC8.16 (VCC), SV1.2; also elsewhere on the board
BT_RST: IC7.17 (RES); also elsewhere on the board
FROM_TX_RS232_M: IC8.13 (R1IN), J12.2
GND: C33.1, C34.1, IC7.1 (GND), IC7.14 (GND), IC7.15 (GND), IC7.28 (GND), IC8.8 (R2IN), IC8.10 (T2IN), IC8.15 (GND), J12.1, J13.3, SV1.1, SV1.4; also elsewhere on the board
I2C_SCL_(5V): J13.2; also elsewhere on the board
I2C_SDA_(5V): J13.1; also elsewhere on the board
MISO: SV1.7; also elsewhere on the board
MOSI: SV1.6; also elsewhere on the board
unnamed: IC7.5 (NRTS), IC7.10 (NCTS)
unnamed: C30.2, IC8.1 (C1+)
unnamed: C30.1, IC8.3 (C1-)
unnamed: C31.2, IC8.4 (C2+)
unnamed: C31.1, IC8.5 (C2-)
unnamed: C32.1, IC8.2 (V+)
unnamed: C33.2, IC8.6 (V-)
RF24_CE: SV1.3; also elsewhere on the board
SCK: SV1.5; also elsewhere on the board
TO_RX_RS232_M: IC8.14 (T1OUT), J12.3
UART_RX: IC7.26 (TXD); also elsewhere on the board
UART_RX_BYPASS: IC7.20 (PIO4), IC8.12 (R1OUT)
UART_TX: IC7.6 (RXD); also elsewhere on the board
UART_TX_BYPASS: IC7.19 (PIO7), IC8.11 (T1IN)

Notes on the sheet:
Communication interfaces (RS232, BT, I2C and SPI/RF24)

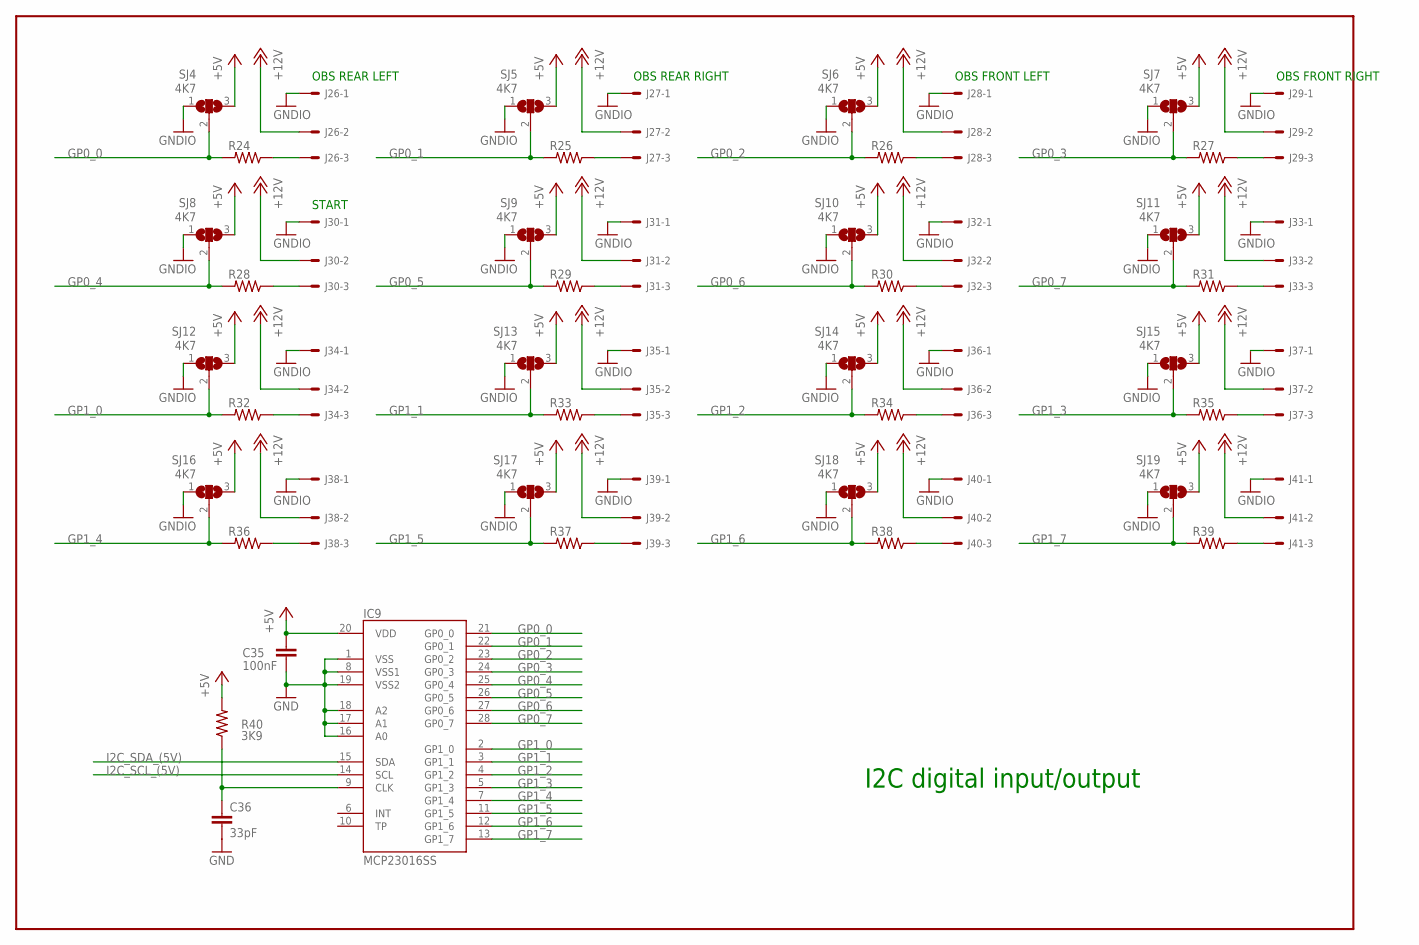
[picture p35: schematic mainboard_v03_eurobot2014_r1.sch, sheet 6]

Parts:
C35: 100nF; C0805
C36: 33pF; C0805
IC9: MCP23016SS; SSOP28
J26, J27, J28, J29, J30, J31, J32, J33, J34, J35, J36, J37, J38, J39, J40, J41: 22-27-2031-03; 6410-03
R24, R25, R26, R27, R28, R29, R30, R31, R32, R33, R34, R35, R36, R37, R38, R39: R-US_R0805; R0805
R40: 3K9; R0805
SJ4, SJ5, SJ6, SJ7, SJ8, SJ9, SJ10, SJ11, SJ12, SJ13, SJ14, SJ15, SJ16, SJ17, SJ18, SJ19: 4K7; SJ_2

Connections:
+5V: C35.1, IC9.20 (VDD), R40.2, SJ4.3, SJ5.3, SJ6.3, SJ7.3, SJ8.3, SJ9.3, SJ10.3, SJ11.3, SJ12.3, SJ13.3, SJ14.3, SJ15.3, SJ16.3, SJ17.3, SJ18.3, SJ19.3; also elsewhere on the board
+12V: J26.2, J27.2, J28.2, J29.2, J30.2, J31.2, J32.2, J33.2, J34.2, J35.2, J36.2, J37.2, J38.2, J39.2, J40.2, J41.2; also elsewhere on the board
GND: C35.2, C36.2, IC9.1 (VSS), IC9.8 (VSS1), IC9.16 (A0), IC9.17 (A1), IC9.18 (A2), IC9.19 (VSS2); also elsewhere on the board
GNDIO: J26.1, J27.1, J28.1, J29.1, J30.1, J31.1, J32.1, J33.1, J34.1, J35.1, J36.1, J37.1, J38.1, J39.1, J40.1, J41.1, SJ4.1, SJ5.1, SJ6.1, SJ7.1, SJ8.1, SJ9.1, SJ10.1, SJ11.1, SJ12.1, SJ13.1, SJ14.1, SJ15.1, SJ16.1, SJ17.1, SJ18.1, SJ19.1; also elsewhere on the board
GP0_0: IC9.21 (GP0_0), R24.2, SJ4.2
GP0_1: IC9.22 (GP0_1), R25.2, SJ5.2
GP0_2: IC9.23 (GP0_2), R26.2, SJ6.2
GP0_3: IC9.24 (GP0_3), R27.2, SJ7.2
GP0_4: IC9.25 (GP0_4), R28.2, SJ8.2
GP0_5: IC9.26 (GP0_5), R29.2, SJ9.2
GP0_6: IC9.27 (GP0_6), R30.2, SJ10.2
GP0_7: IC9.28 (GP0_7), R31.2, SJ11.2
GP1_0: IC9.2 (GP1_0), R32.2, SJ12.2
GP1_1: IC9.3 (GP1_1), R33.2, SJ13.2
GP1_2: IC9.4 (GP1_2), R34.2, SJ14.2
GP1_3: IC9.5 (GP1_3), R35.2, SJ15.2
GP1_4: IC9.7 (GP1_4), R36.2, SJ16.2
GP1_5: IC9.11 (GP1_5), R37.2, SJ17.2
GP1_6: IC9.12 (GP1_6), R38.2, SJ18.2
GP1_7: IC9.13 (GP1_7), R39.2, SJ19.2
I2C_SCL_(5V): IC9.14 (SCL); also elsewhere on the board
I2C_SDA_(5V): IC9.15 (SDA); also elsewhere on the board
unnamed: J26.3, R24.1
unnamed: J30.3, R28.1
unnamed: J27.3, R25.1
unnamed: J31.3, R29.1
unnamed: J34.3, R32.1
unnamed: J38.3, R36.1
unnamed: J35.3, R33.1
unnamed: J39.3, R37.1
unnamed: J40.3, R38.1
unnamed: J36.3, R34.1
unnamed: J37.3, R35.1
unnamed: J41.3, R39.1
unnamed: J32.3, R30.1
unnamed: J33.3, R31.1
unnamed: J29.3, R27.1
unnamed: J28.3, R26.1
unnamed: C36.1, IC9.9 (CLK), R40.1

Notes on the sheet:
I2C digital input/output
OBS FRONT LEFT
OBS FRONT RIGHT
OBS REAR LEFT
OBS REAR RIGHT
START

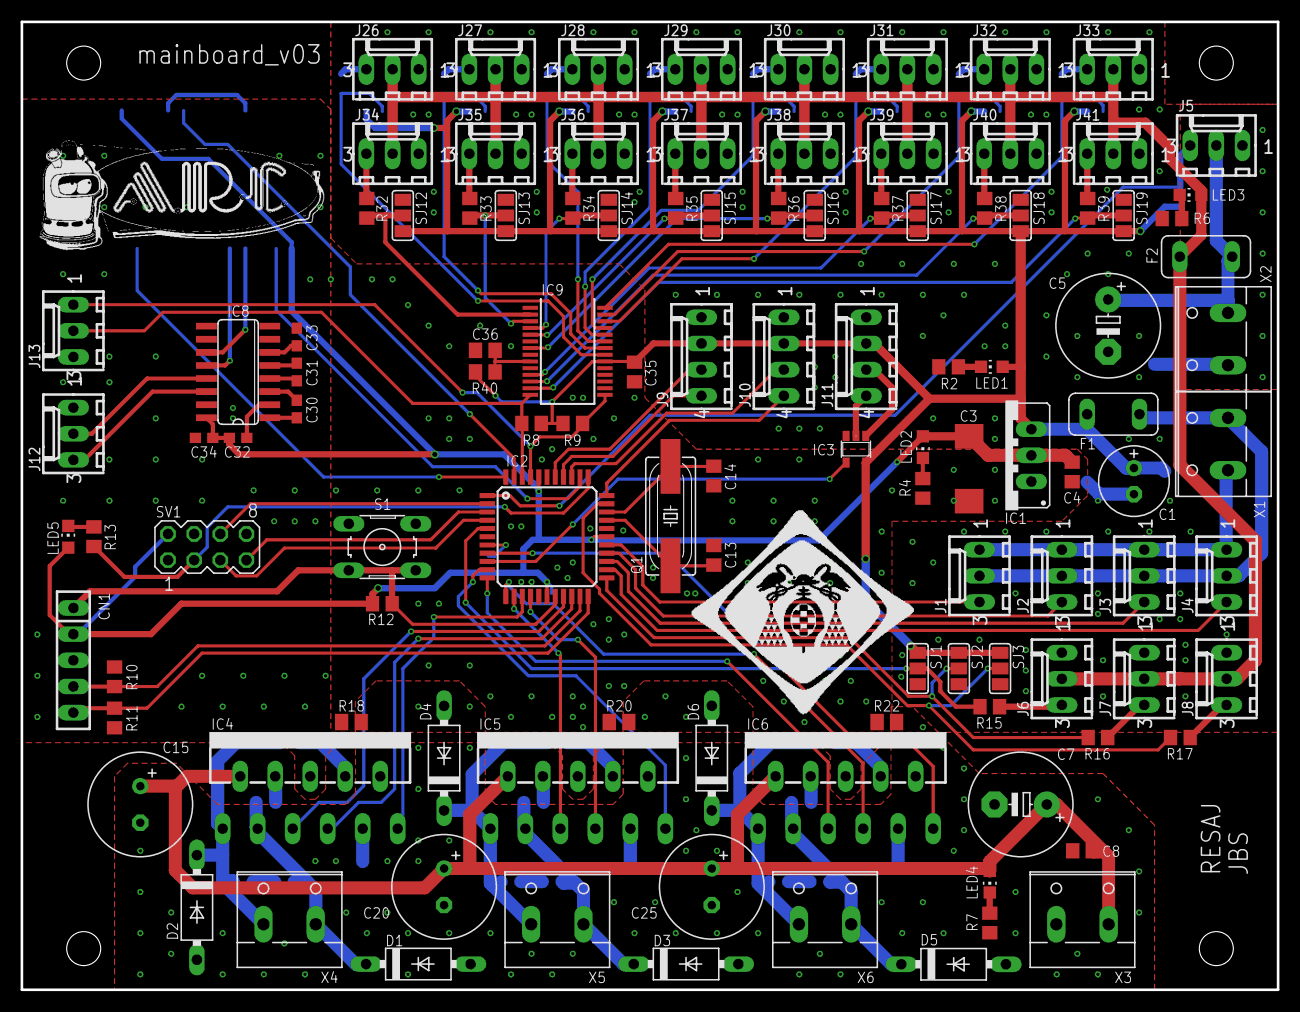
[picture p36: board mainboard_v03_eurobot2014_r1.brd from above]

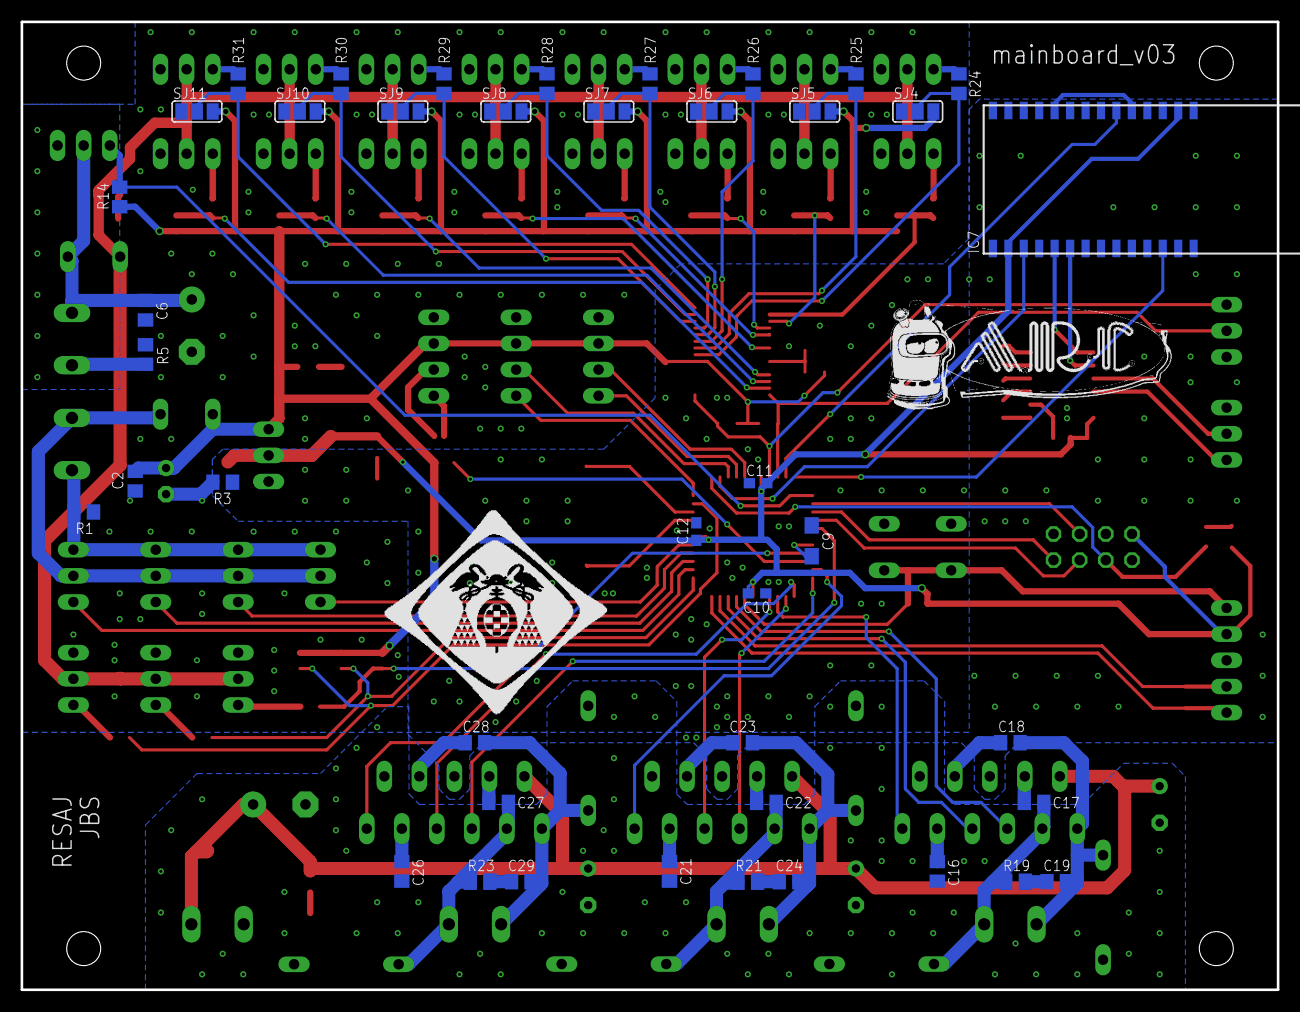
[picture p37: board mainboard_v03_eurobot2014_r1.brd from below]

Board: 2 copper layers, 122.0 x 94.0 mm, 160 parts (44 on the bottom side), 120 nets.

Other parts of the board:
U$1, U$2: LOGO_ARC_28MM
U$3, U$4: LOGO_IEEE_22MM

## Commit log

2016-03-01 Creado fichero de ignorados.
2016-03-01 Añadida fuente de alimentación ATX y completado README.
2016-03-01 Añadido el resto de tarjetas.
    [DESIGN1.DSN, bom.xls, bom_dk.csv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]
2016-03-01 Añadida imagen de licencia CC.
2016-03-07 Añadidas fotos de las tarjetas.
2016-03-10 Dimensiones de imagenes re-escaladas, actualizado readme.
2016-03-10 Fotos de tarjetas modificadas.
2016-03-10 Nueva foto de la sensorboard.
2016-03-10 Modificado dimensiones de la foto de la switchboard.
